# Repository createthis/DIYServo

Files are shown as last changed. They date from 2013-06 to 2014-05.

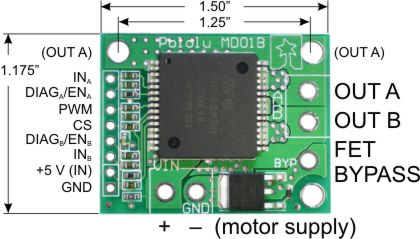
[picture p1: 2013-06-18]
docs/pololu_mdb01_pinout.jpg

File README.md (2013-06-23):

DIYServo
========

http://www.diyservo.com

DIY Servo Project - Create your own servo using any motor of your choosing

This servo uses an Arduino Nano as a controller, and a Pololu MD01B as a motor driver.
The prototype uses a Banebots P60 gearbox (planetary gearing) mated to an RS555 motor. Substitute any 12V motor
of your choosing. For example, a 12V windshield wiper motor (worm gear) would work, or smaller hobby robotics
motors.

Video of latest gear driven MRE in action:
http://youtu.be/2uWNyV8dUlA

Older video of bearing plate mounted MRE in action:
http://youtu.be/V_V_hvIjvC8

Bill of Materials (BOM): https://docs.google.com/spreadsheet/ccc?key=0AlOm0VEWX2qMdGIxMThxUHNPeFVPeEotaU9RSDRENGc&usp=sharing

<br />This work is licensed under a <a rel="license" href="http://creativecommons.org/licenses/by-sa/3.0/">Creative Commons Attribution-ShareAlike 3.0 Unported License</a>.

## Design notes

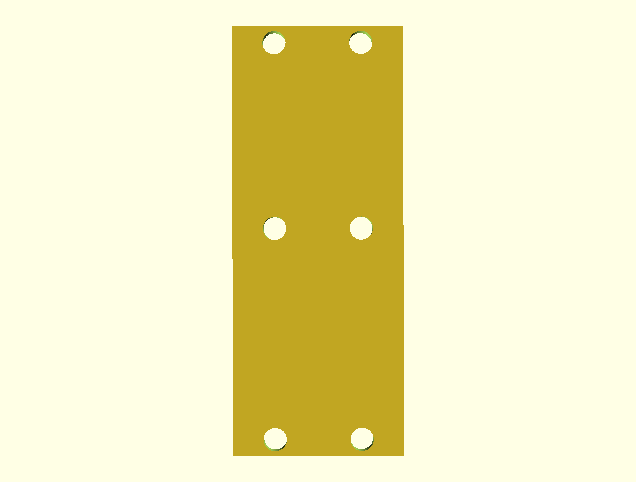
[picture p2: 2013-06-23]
OpenSCAD/motor_plate/motor_plate.png

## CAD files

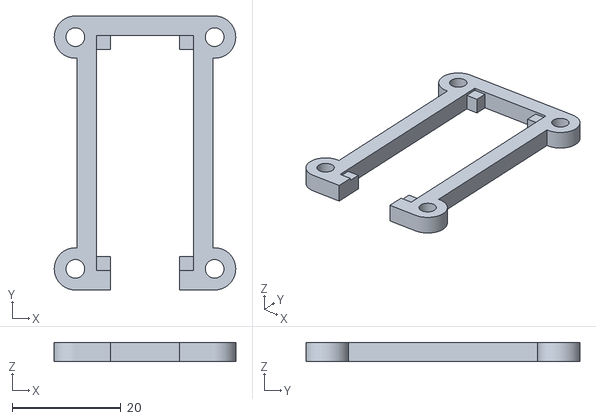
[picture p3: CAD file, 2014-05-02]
OpenSCAD/arduino_nano_enclosure/arduino_nano_enclosure_lid.stl
33.4 x 50.4 x 3.57

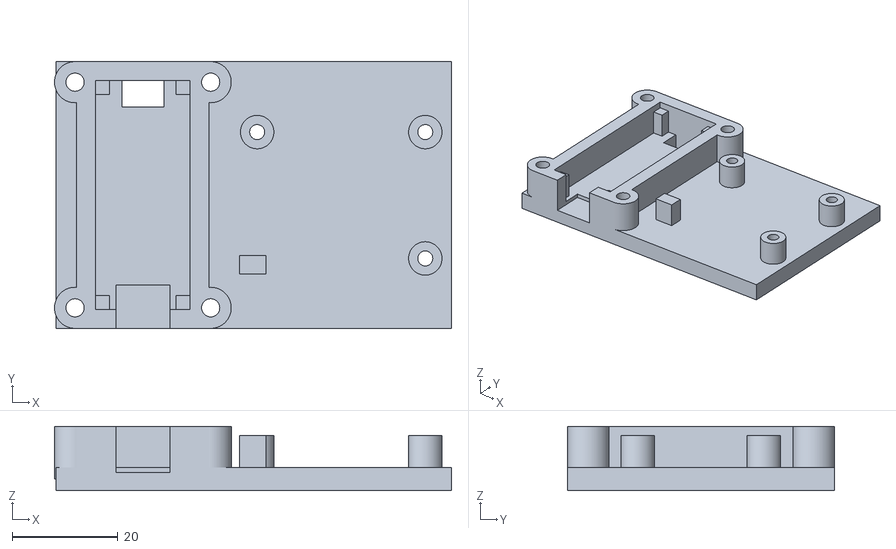
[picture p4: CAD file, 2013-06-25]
OpenSCAD/arduino_nano_pololu_md01b_mounting_plate/arduino_nano_pololu_md01b_mounting_plate_90_center.stl
75.0 x 50.4 x 12.1

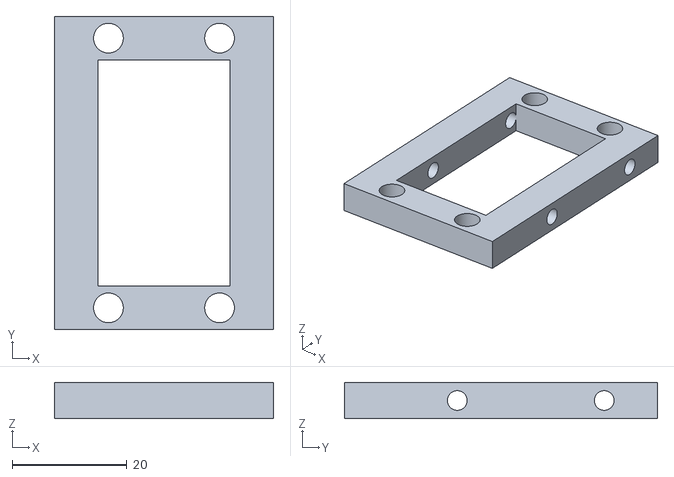
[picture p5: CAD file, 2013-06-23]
OpenSCAD/motor_plate/motor_plate_mounting_bracket.stl
38.2 x 54.6 x 6.29

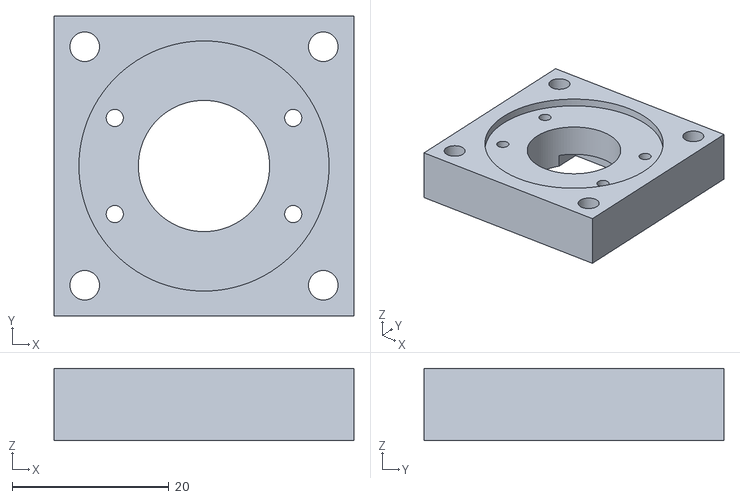
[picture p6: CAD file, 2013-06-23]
OpenSCAD/motor_plate_front/motor_plate_front.stl
38.3 x 38.3 x 9.25

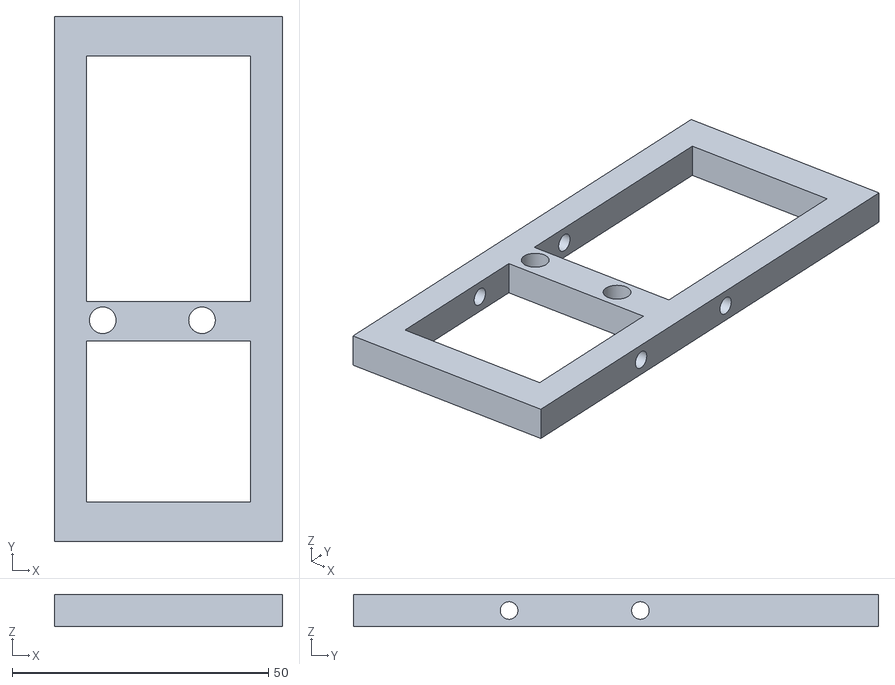
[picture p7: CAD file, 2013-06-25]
OpenSCAD/motor_plate_side/motor_plate_side.stl
44.5 x 102.5 x 6.29

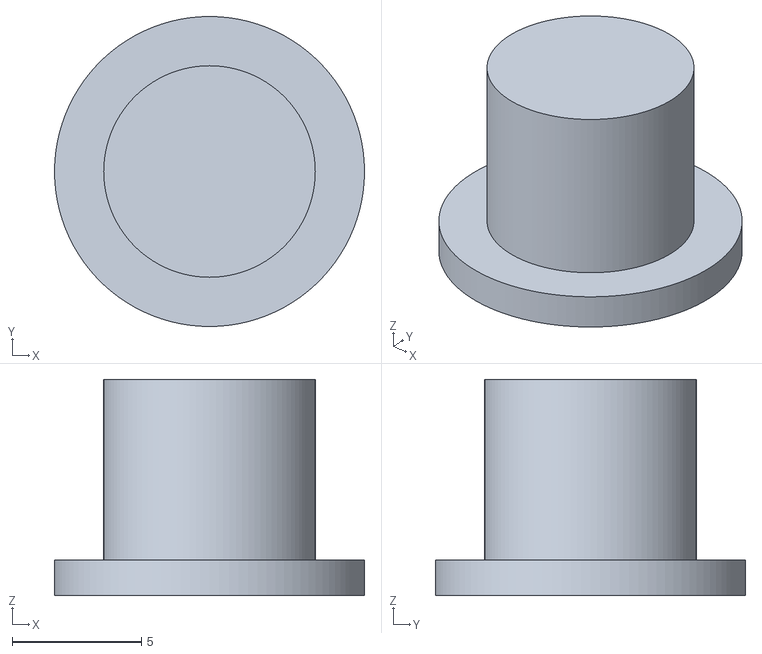
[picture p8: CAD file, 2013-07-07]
OpenSCAD/mre_gear_box/mre_gear_plug.stl
12.0 x 12.0 x 8.38

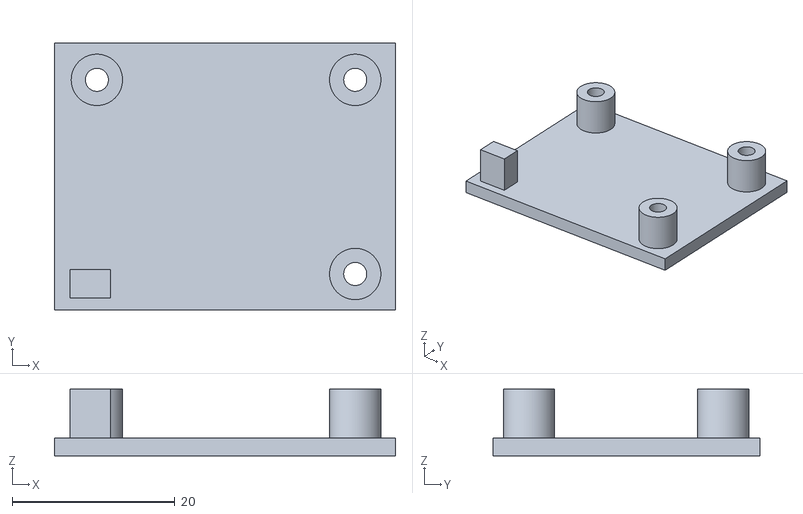
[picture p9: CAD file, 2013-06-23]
OpenSCAD/pololu_md01b_mounting_plate/pololu_md01b_mounting_plate.stl
41.9 x 32.8 x 8.20

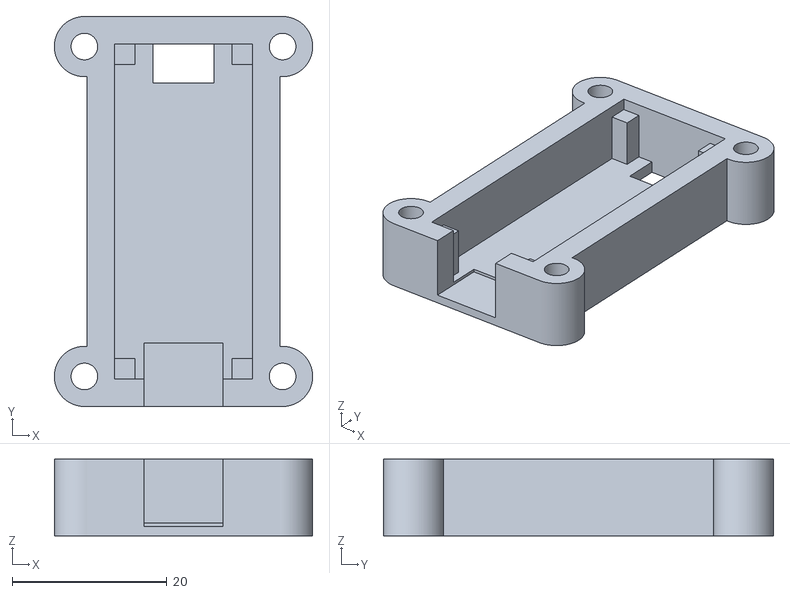
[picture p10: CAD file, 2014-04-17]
OpenSCAD/arduino_nano_enclosure/arduino_nano_enclosure.stl
33.4 x 50.4 x 9.94

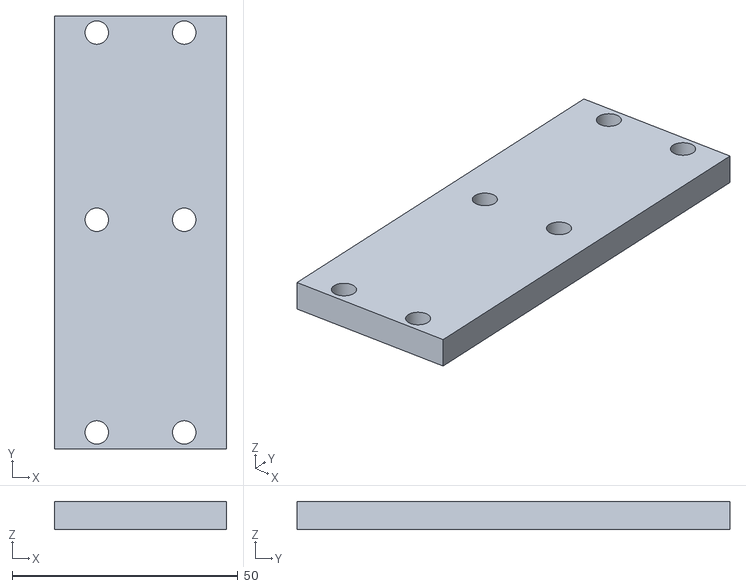
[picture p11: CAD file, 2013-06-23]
OpenSCAD/motor_plate/motor_plate.stl
38.2 x 95.9 x 6.29

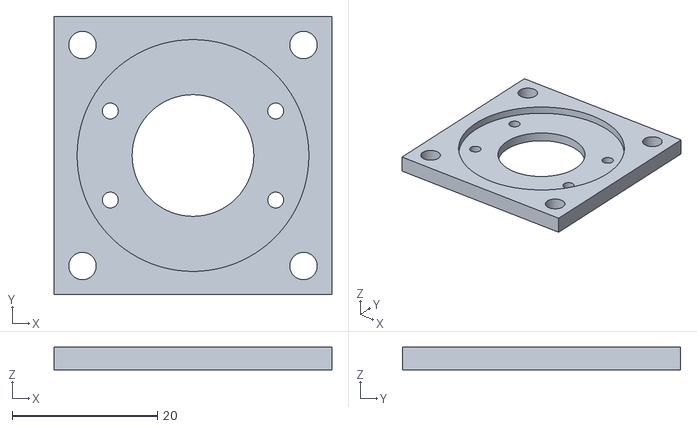
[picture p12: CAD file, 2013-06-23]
OpenSCAD/motor_plate_front/motor_plate_front_bottom.stl
38.3 x 38.3 x 3.12

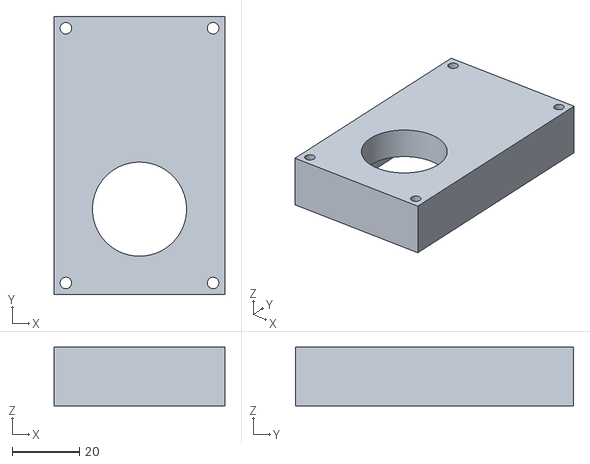
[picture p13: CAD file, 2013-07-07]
OpenSCAD/mre_gear_box/gearbox_cover.stl
50.8 x 82.8 x 17.6

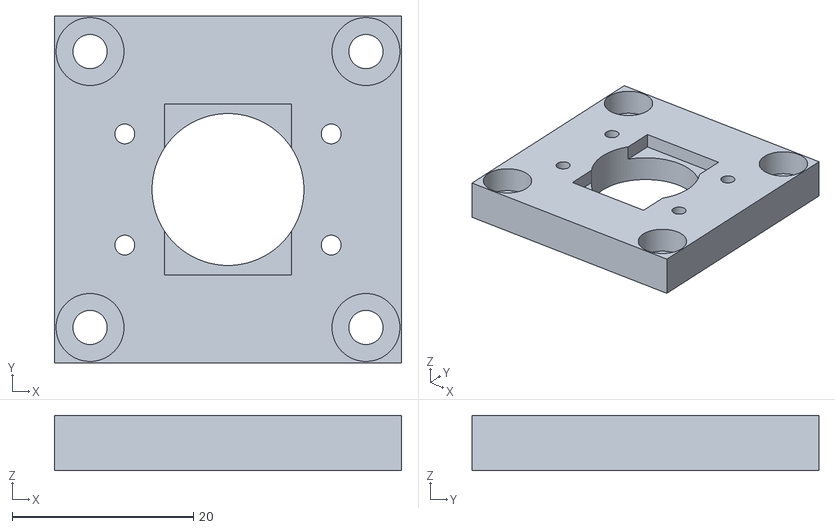
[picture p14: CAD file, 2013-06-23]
OpenSCAD/motor_plate_front/motor_plate_front_top.stl
38.3 x 38.3 x 6.12

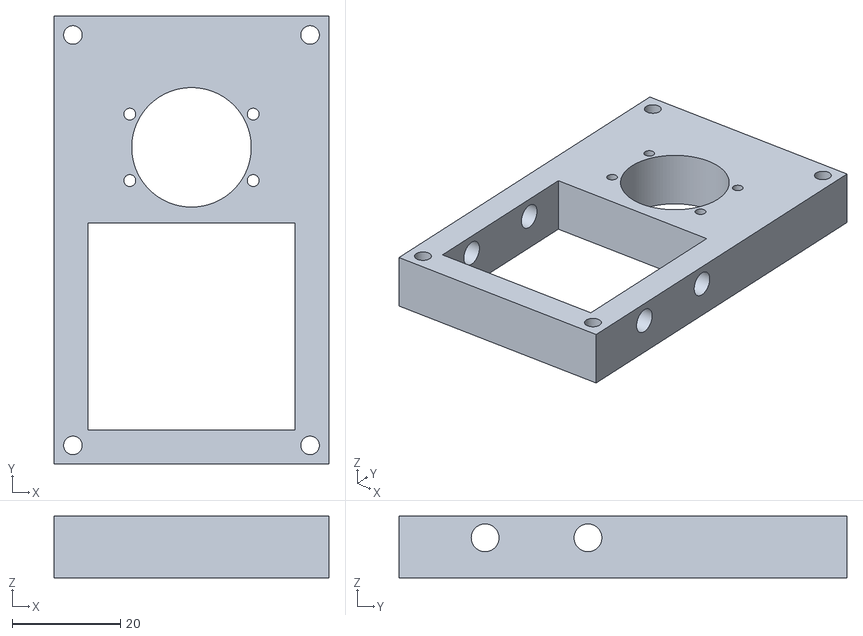
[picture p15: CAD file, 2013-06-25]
OpenSCAD/mre_gear_box/bearing_block.stl
50.8 x 82.8 x 11.4

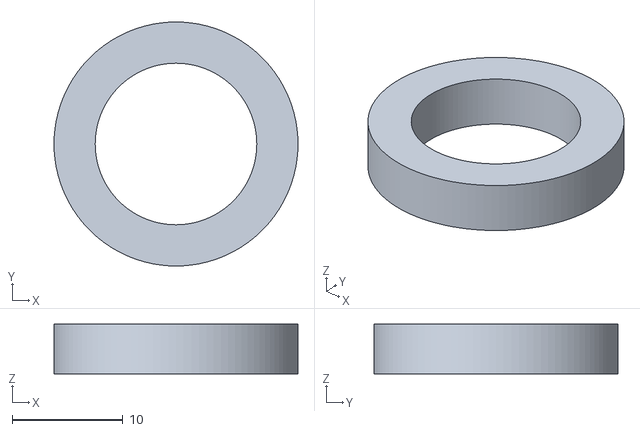
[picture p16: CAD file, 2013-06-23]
OpenSCAD/mre_gear_box/bearing_spacer.stl
22.1 x 22.1 x 4.48

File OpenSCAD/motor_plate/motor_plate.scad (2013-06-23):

/* Copyright 2013 CreateThis.com
 * All Rights Reserved
 */

include <../resolution.scad>
include <motor_plate_dimensions.scad>

// Do It
difference(){
  cube(size = [dimension_width,dimension_length,dimension_thickness], center = true);

  // holes

  // top
  // right
  translate(v = [ dimension_width_center_to_hole_right,dimension_length_middle_to_top_hole_center,0]) {
    cylinder(h = dimension_thickness,r = dimension_hole_radius_scaled,center = true, $fn = resolution);
  }
  // left
  translate(v = [ -dimension_width_center_to_hole_right,dimension_length_middle_to_top_hole_center,0]) {
    cylinder(h = dimension_thickness,r = dimension_hole_radius_scaled,center = true, $fn = resolution);
  }

  // bottom
  // right
  translate(v = [ dimension_width_center_to_hole_right,-dimension_length_middle_to_top_hole_center,0]) {
    cylinder(h = dimension_thickness,r = dimension_hole_radius_scaled,center = true, $fn = resolution);
  }
  // left
  translate(v = [ -dimension_width_center_to_hole_right,-dimension_length_middle_to_top_hole_center,0]) {
    cylinder(h = dimension_thickness,r = dimension_hole_radius_scaled,center = true, $fn = resolution);
  }

  // middle
  // right
  translate(v = [ dimension_width_center_to_hole_right,dimension_length_middle_to_middle_hole_center,0]) {
    cylinder(h = dimension_thickness,r = dimension_hole_radius_scaled,center = true, $fn = resolution);
  }
  // left
  translate(v = [ -dimension_width_center_to_hole_right,dimension_length_middle_to_middle_hole_center,0]) {
    cylinder(h = dimension_thickness,r = dimension_hole_radius_scaled,center = true, $fn = resolution);
  }
}

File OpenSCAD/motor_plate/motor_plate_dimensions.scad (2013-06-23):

/* Copyright 2013 CreateThis.com
 * All Rights Reserved
 */

include <../resolution.scad>

/* Motor plate looks like this:
 *
 * +------+
 * |o    o| top
 * |      |
 * |      |
 * |o    o| middle
 * |      |
 * |      |
 * |      |
 * |o    o| bottom
 * +------+
 */

// Measured Dimensions
dimension_width = 38.18;
dimension_length = 95.94;
dimension_thickness = 6.29;
dimension_hole_diameter = 4.71; // This accepts a #10-32 x 1/2" screw.
dimension_top_to_hole = 1.32;
dimension_side_to_hole = 7.05;
dimension_middle_top_to_hole = 1.42;
dimension_bottom_to_middle_top = 54.57;
dimension_middle_plate_length = 7.58;
dimension_side_screw_hole_diameter = 3.43; // This accepts a #6-32 screw

// Calculated Dimensions Big Plate
dimension_hole_diameter_scaled = dimension_hole_diameter * 1.10; // Add 10% to compensate for printer overflow
dimension_hole_radius = dimension_hole_diameter / 2;
dimension_hole_radius_scaled = dimension_hole_diameter_scaled / 2;
dimension_length_middle_to_top_hole_center = dimension_length / 2 - (dimension_top_to_hole + dimension_hole_radius);
dimension_length_middle_to_middle_hole_center = (dimension_bottom_to_middle_top - dimension_middle_top_to_hole - dimension_hole_radius) - dimension_length / 2;
dimension_width_center_to_hole_right = dimension_width / 2 - dimension_side_to_hole - dimension_hole_radius;

// Calculated Dimensions Gearbox Plate
dimension_gearbox_length = dimension_bottom_to_middle_top;
dimension_gearbox_middle_to_top_hole_center = dimension_gearbox_length / 2 - (dimension_middle_top_to_hole + dimension_hole_radius);
dimension_side_screw_hole_radius = dimension_side_screw_hole_diameter / 2;
dimension_gearbox_through_hole_y = dimension_gearbox_length / 2 - dimension_middle_plate_length - dimension_side_screw_hole_radius;

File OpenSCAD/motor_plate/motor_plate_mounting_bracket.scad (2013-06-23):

/* Copyright 2013 CreateThis.com
 * All Rights Reserved
 */

include <../resolution.scad>
include <motor_plate_dimensions.scad>
use <../arduino_nano_enclosure/arduino_nano_enclosure.scad>

// Do It
difference(){
  cube(size = [dimension_width,dimension_gearbox_length,dimension_thickness], center = true);

  // holes

  // bottom
  // right
  translate(v = [ dimension_width_center_to_hole_right,-dimension_gearbox_middle_to_top_hole_center,0]) {
    cylinder(h = dimension_thickness,r = dimension_hole_radius_scaled,center = true, $fn = resolution);
  }
  // left
  translate(v = [ -dimension_width_center_to_hole_right,-dimension_gearbox_middle_to_top_hole_center,0]) {
    cylinder(h = dimension_thickness,r = dimension_hole_radius_scaled,center = true, $fn = resolution);
  }

  // middle
  // right
  translate(v = [ dimension_width_center_to_hole_right,dimension_gearbox_middle_to_top_hole_center,0]) {
    cylinder(h = dimension_thickness,r = dimension_hole_radius_scaled,center = true, $fn = resolution);
  }
  // left
  translate(v = [ -dimension_width_center_to_hole_right,dimension_gearbox_middle_to_top_hole_center,0]) {
    cylinder(h = dimension_thickness,r = dimension_hole_radius_scaled,center = true, $fn = resolution);
  }

  // side top
  translate(v = [0,dimension_gearbox_through_hole_y,0]) {
    rotate(a=90, v=[0,1,0]) {
      cylinder(h = dimension_width + 0.0001 /* OpenSCAD math bug */,r = dimension_side_screw_hole_radius,center = true, $fn = resolution);
    }
  }

  translate(v = [0,dimension_gearbox_through_hole_y - arduino_nano_enclosure_distance_between_holes_width(),0]) {
    rotate(a=90, v=[0,1,0]) {
      cylinder(h = dimension_width + 0.0001 /* OpenSCAD math bug */,r = dimension_side_screw_hole_radius,center = true, $fn = resolution);
    }
  }

  // Cut hole in middle for faster print times and less waste
  cube(size = [dimension_width - dimension_middle_plate_length * 2,dimension_gearbox_length - dimension_middle_plate_length * 2,dimension_thickness], center = true);
}

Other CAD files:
OpenSCAD/mre_gear_box/bearing_spacer_plate.stl
OpenSCAD/mre_gear_box/mre_gear.stl
OpenSCAD/mre_gear_box/output_shaft_gear.stl
OpenSCAD/motor_plate_front/motor_plate_front.scad
OpenSCAD/arduino_nano_enclosure/arduino_nano_enclosure.scad
OpenSCAD/arduino_nano_enclosure/arduino_nano_enclosure_dimensions.scad
OpenSCAD/arduino_nano_enclosure/arduino_nano_enclosure_lid.scad
OpenSCAD/arduino_nano_pololu_md01b_mounting_plate/arduino_nano_pololu_md01b_mounting_plate_90.scad
OpenSCAD/arduino_nano_pololu_md01b_mounting_plate/arduino_nano_pololu_md01b_mounting_plate_90_center.scad
OpenSCAD/banebots/p60.scad
OpenSCAD/motor_plate_side/motor_plate_side.scad
OpenSCAD/mre_gear_box/bearing_block.scad
OpenSCAD/mre_gear_box/bearing_block_dimensions.scad
OpenSCAD/mre_gear_box/bearing_spacer.scad
OpenSCAD/mre_gear_box/bearing_spacer_plate.scad
OpenSCAD/mre_gear_box/gear_dimensions.scad
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

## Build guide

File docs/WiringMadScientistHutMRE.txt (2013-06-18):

I've gotten an AS5040 10-bit magnetic rotary encoder, and an AS5045 12-bit, working, checking all the non-programmed interfaces. Both can be one-time programmed to output different code schemes, but they're not very useful for what I need so I'm not messing with them.
In both cases I piggybacked the chip/breakout board off an Arduino, using the 3.3v supply. I rather randomly chose to use pins 2, 6, and 7 of the Arduino for the digital input: 6 is a chip select that also signals the start of an interface round, 7 acts as the clock from the Arduino to the chip, and 2 acts as the data transfer from the chip to the Arduino. These are trivially remapped.
The code includes a debug setting that'll print out any faults the AS504x notices, but if you turn off the debug setting you'll just get degrees out. It reads from the chip and transmits to the host computer roughly once a second.

-- John, Mon Dec 13, 2010 11:14 pm
   http://www.madscientisthut.com

More succinctly:
  Arduino Nano - AS5040 Board
           GND - GND
           3v3 - VCC (+3.3v)
             2 - SD Out
             6 - CSEL
             7 - CLK_IN

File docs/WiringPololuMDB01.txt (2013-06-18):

Arduino Nano - Pololu MDB01
          10 - INa
          11 - PWM
          12 - INb
          5V - +5V (IN)
         GND - GND

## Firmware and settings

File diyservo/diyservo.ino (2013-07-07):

/*
   DIY Servo - Arduino driving VNH2SP30 Motor Driver Carrier MD01B

   This work is licensed under the Creative Commons Attribution-ShareAlike 3.0 Unported License. To view a copy of this license, visit http://creativecommons.org/licenses/by-sa/3.0/ or send a letter to Creative Commons, 444 Castro Street, Suite 900, Mountain View, California, 94041, USA.
 */

#include <PololuDriver.h>
#include <PID_v1.h>
#include <PID_AutoTune_v0.h>

#define ENCODER_A_PIN 2
#define ENCODER_B_PIN 3

// PID Variables
double currentPosition = 310;
double distance = 0; // distance in degrees from currentPosition to positionGoal
double distanceGoal = 0; // we always want the motor to be right on the money
double motorSpeed = 0;
double positionGoal = 120;
double kp=0.000001, ki=0, kd=40;
/* kd=0.005 kind of stable */
double upperSpeedLimit = 255;
double lowerSpeedLimit = 33;

// AutoTune Library Variables
double aTuneStep=80, aTuneNoise=1, aTuneStartValue=(upperSpeedLimit - lowerSpeedLimit) / 2 + lowerSpeedLimit;
unsigned int aTuneLookBack=20;
byte ATuneModeRemember=2;

PololuDriver myPololuDriver(11,10,12); // initialize instance of class

const int ledPin = 13; //LED connected to digital pin 13
const int clockPin = 7; //output to clock
const int CSnPin = 6; //output to chip select
const int inputPin = 2; //read AS5040

int debug = 1; //SET THIS TO 0 TO DISABLE PRINTING OF ERROR CODES
boolean tuning = false; // Set this to true to autotune PID values

String currentState = "stop";
String lastState = "stop";
long lastAngle = 0;

//Specify the links and initial tuning parameters
PID myPID(&distance, &motorSpeed, &distanceGoal,kp,ki,kd, DIRECT);
PID_ATune aTune(&currentPosition, &motorSpeed);

// the setup routine runs once when you press reset:
void setup() { 
  Serial.begin(19200);
  Serial.setTimeout(50);
  Serial.println("Started");

  pinMode(ENCODER_A_PIN, INPUT);
  pinMode(ENCODER_B_PIN, INPUT);

  pinMode(ledPin, OUTPUT); // visual signal of I/O to chip
  pinMode(clockPin, OUTPUT); // SCK
  pinMode(CSnPin, OUTPUT); // CSn -- has to toggle high and low to signal chip to start data transfer
  pinMode(inputPin, INPUT); // SDA

  myPololuDriver.Run(POLOLU_STOP);

  currentPosition = read_angle();

  //turn the PID on
  myPID.SetMode(AUTOMATIC);
  myPID.SetOutputLimits(lowerSpeedLimit,upperSpeedLimit);

  if(tuning)
  {
    tuning=false;
    changeAutoTune();
    tuning=true;
    Serial.println("tuning mode");
  }
}

long angle_diff(long angle1, long angle2) {
  return (abs(angle1 + 180 - angle2) % 360 - 180); 
}

boolean should_go_forward(long angle1, long angle2) {
  return ((angle1 - angle2 + 360)%360>180);
}

// the loop routine runs over and over again forever:
void loop() {
  lastState = currentState;

  currentPosition = read_angle();
  distance = abs(angle_diff(currentPosition, positionGoal));

  if(tuning)
  {
    byte val = (aTune.Runtime());
    if (val!=0)
    {
      tuning = false;
    }
    if(!tuning)
    { //we're done, set the tuning parameters
      kp = aTune.GetKp();
      ki = aTune.GetKi();
      kd = aTune.GetKd();
      myPID.SetTunings(kp,ki,kd);
      AutoTuneHelper(false);
      Serial.print("kp: ");Serial.print(myPID.GetKp());Serial.print(" ");
      Serial.print("ki: ");Serial.print(myPID.GetKi());Serial.print(" ");
      Serial.print("kd: ");Serial.print(myPID.GetKd());Serial.println();
    }
  }
  else myPID.Compute();

  myPololuDriver.SetSpeed((byte) motorSpeed);

  // send data only when you receive data:
  if (Serial.available() > 0) {
    myPololuDriver.Run(POLOLU_STOP);
    currentState = "stop";
    lastState = "stop";
    // read the incoming byte:
    positionGoal = (double) Serial.parseInt();

    // say what you got:
    Serial.print("I received: ");
    Serial.println(positionGoal, DEC);
    Serial.print("myangle: ");
    Serial.println(currentPosition, DEC);

    //if((positionGoal==0 && !tuning) || (positionGoal!=0 && tuning))changeAutoTune();
  } else {
    if (abs(angle_diff(lastAngle,currentPosition)) > 1) {
      //Serial.print("angle_diff: ");
      //Serial.println(angle_diff(currentPosition, positionGoal), DEC);
    }

    if(tuning){
      //Serial.println("tuning mode");
    }
  }

  if (abs(angle_diff(currentPosition, positionGoal)) == 0 /* 0 degree hysterisis */) {
    if (lastState != "stop") {
/*
      Serial.println("stop");
      Serial.print("currentPosition: ");
      Serial.println(currentPosition, DEC);
*/
      myPololuDriver.SetSpeed((byte)motorSpeed);
      currentState = "stop";
      myPololuDriver.Run(POLOLU_STOP);
    }
  } else {
    if (!should_go_forward(currentPosition, positionGoal)) {
/*
      Serial.print("should go forward");
      Serial.print(",distance=");
      Serial.print(distance,DEC);
      Serial.print(",motorSpeed=");
      Serial.print(motorSpeed,DEC);
      Serial.print(",currentPosition=");
      Serial.print(currentPosition,DEC);
      Serial.print(",positionGoal=");
      Serial.println(positionGoal,DEC);
*/
      if (lastState != "forward") {
//        Serial.println("forward");
        myPololuDriver.SetSpeed((byte)motorSpeed);
        currentState = "forward";
        myPololuDriver.Run(POLOLU_FORWARD);
      }
    } else {
/*
      Serial.print("should reverse");
      Serial.print(",distance=");
      Serial.print(distance,DEC);
      Serial.print(",motorSpeed=");
      Serial.print(motorSpeed,DEC);
      Serial.print(",currentPosition=");
      Serial.print(currentPosition,DEC);
      Serial.print(",positionGoal=");
      Serial.println(positionGoal,DEC);
*/

      if (lastState != "reverse") {
//        Serial.println("reverse");
        myPololuDriver.SetSpeed((byte)motorSpeed);
        currentState = "reverse";
        myPololuDriver.Run(POLOLU_REVERSE);
      }
    }
  }
  lastAngle = currentPosition;
}

long read_angle()
{
  int inputstream = 0; //one bit read from pin
  long packeddata = 0; //two bytes concatenated from inputstream
  long angle = 0; //holds processed angle value
  long anglemask = 65472; //0x1111111111000000: mask to obtain first 10 digits with position info
  long statusmask = 63; //0x000000000111111; mask to obtain last 6 digits containing status info
  long statusbits; //holds status/error information
  int DECn; //bit holding decreasing magnet field error data
  int INCn; //bit holding increasing magnet field error data
  int OCF; //bit holding startup-valid bit
  int COF; //bit holding cordic DSP processing error data
  int LIN; //bit holding magnet field displacement error data
  int shortdelay = 40; // this is the microseconds of delay in the data clock
  int longdelay = 1; // this is the milliseconds between readings

  // CSn needs to cycle from high to low to initiate transfer. Then clock cycles. As it goes high
  // again, data will appear on sda
  digitalWrite(CSnPin, HIGH); // CSn high
  digitalWrite(clockPin, HIGH); // CLK high
  //delay(longdelay);// time between readings
  delayMicroseconds(shortdelay); // delay for chip initialization
  digitalWrite(ledPin, HIGH); // signal start of transfer with LED
  digitalWrite(CSnPin, LOW); // CSn low: start of transfer
  delayMicroseconds(shortdelay); // delay for chip initialization
  digitalWrite(clockPin, LOW); // CLK goes low: start clocking
  delayMicroseconds(shortdelay); // hold low
  for (int x=0; x <16; x++) // clock signal, 16 transitions, output to clock pin
  {
    digitalWrite(clockPin, HIGH); //clock goes high
    delayMicroseconds(shortdelay); // 
    inputstream =digitalRead(inputPin); // read one bit of data from pin
    //Serial.print(inputstream, DEC);
    packeddata = ((packeddata << 1) + inputstream);// left-shift summing variable, add pin value
    digitalWrite(clockPin, LOW);
    delayMicroseconds(shortdelay); // end of one clock cycle
  }
  // end of entire clock cycle
  //Serial.println(" ");
  digitalWrite(ledPin, LOW); // signal end of transmission
  // lots of diagnostics for verifying bitwise operations
  //Serial.print("packed:");
  //Serial.println(packeddata,DEC);
  //Serial.print("pack bin: ");
  // Serial.println(packeddata,BIN);
  angle = packeddata & anglemask; // mask rightmost 6 digits of packeddata to zero, into angle.
  //Serial.print("mask: ");
  //Serial.println(anglemask, BIN);
  //Serial.print("bin angle:");
  //Serial.println(angle, BIN);
  //Serial.print("angle: ");
  //Serial.println(angle, DEC);
  angle = (angle >> 6); // shift 16-digit angle right 6 digits to form 10-digit value
  //Serial.print("angleshft:");
  //Serial.println(angle, BIN);
  //Serial.print("angledec: ");
  //Serial.println(angle, DEC);
  angle = angle * 0.3515; // angle * (360/1024) == actual degrees
  //Serial.print("angle: "); // and, finally, print it.
  //Serial.println(angle, DEC);
  //Serial.println("--------------------");
  //Serial.print("raw: "); // this was the prefix for the bit-by-bit diag output inside the loop.
  if (debug)
  {
    statusbits = packeddata & statusmask;
    DECn = statusbits & 2; // goes high if magnet moved away from IC
    INCn = statusbits & 4; // goes high if magnet moved towards IC
    LIN = statusbits & 8; // goes high for linearity alarm
    COF = statusbits & 16; // goes high for cordic overflow: data invalid
    OCF = statusbits & 32; // this is 1 when the chip startup is finished.
    if (DECn && INCn) { Serial.println("magnet moved out of range"); }
    else
    {
      if (DECn) { Serial.println("magnet moved away from chip"); }
      if (INCn) { Serial.println("magnet moved towards chip"); }
    }
    if (LIN) { Serial.println("linearity alarm: magnet misaligned? Data questionable."); }
    if (COF) { Serial.println("cordic overflow: magnet misaligned? Data invalid."); }
  }

  return (double) angle;

  packeddata = 0; // reset both variables to zero so they don't just accumulate
  angle = 0;
}

void changeAutoTune()
{
  if(!tuning)
  {
    //Set the output to the desired starting frequency.
    motorSpeed=aTuneStartValue;
    aTune.SetNoiseBand(aTuneNoise);
    aTune.SetOutputStep(aTuneStep);
    aTune.SetLookbackSec((int)aTuneLookBack);
    AutoTuneHelper(true);
    tuning = true;
  }
  else
  { //cancel autotune
    aTune.Cancel();
    tuning = false;
    AutoTuneHelper(false);
  }
}

void AutoTuneHelper(boolean start)
{
  if(start)
    ATuneModeRemember = myPID.GetMode();
  else
    myPID.SetMode(ATuneModeRemember);
}

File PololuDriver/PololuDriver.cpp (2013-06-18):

#include "PololuDriver.h"

PololuDriver::PololuDriver(byte pwmPin, byte inA, byte inB)
{
	m_pwm = pwmPin;
	m_inA = inA;
	m_inB = inB;
	
	pinMode(inA, OUTPUT); //can send +/0 voltage 3.3v/0
	pinMode(inB, OUTPUT);
	analogWrite(m_pwm, 0);
}

void PololuDriver::SetSpeed(byte speed)
{	
	analogWrite(m_pwm, speed);
}

void PololuDriver::Run(byte direction)
{	
	switch (direction)
	{
		case POLOLU_STOP:
			digitalWrite(m_inA, LOW);
			digitalWrite(m_inB, LOW);
			break;
		case POLOLU_FORWARD:
			digitalWrite(m_inA, HIGH);
			digitalWrite(m_inB, LOW);
			break;
		case POLOLU_REVERSE	:
			digitalWrite(m_inA, LOW);
			digitalWrite(m_inB, HIGH);
			break;
	}
}

void PololuDriver::Run(byte direction, byte speed)
{
	SetSpeed(speed);
	Run(direction);
}

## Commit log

2013-06-18 add BOM
2013-06-23 Arduino is quirky and requires sketches to be in a directory of the same name. Go figure.
2013-06-23 Add OpenSCAD source code. This is the code necessary to 3d print all of the plastics for the project.
    [arduino_nano_enclosure.scad, arduino_nano_enclosure.stl, arduino_nano_enclosure_dimensions.scad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]
2013-06-24 Add side motor plate
    [bearing_block.scad, motor_plate_side.scad, motor_plate_side.stl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]
2013-06-25 Add a basic modeling of the p60 gearbox. This should help people visualize the dimensions coming from the p60 module.
    [p60.scad]
2013-06-25 tweak the scale factor to compensate for my inaccurate hobby printer
    [motor_plate_side.scad, p60.scad]
2013-06-25 update stl for hobby printer scale factor.
    [motor_plate_side.stl]
2013-06-25 move the md01b to the center of the board so we can add a case later.
    [arduino_nano_enclosure.scad, arduino_nano_pololu_md01b_mounting_plate.scad, arduino_nano_pololu_md01b_mounting_plate.stl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]
2013-06-25 Add bottom and lid mounting holes to bearing plate.
    [bearing_block.scad, bearing_block.stl, bearing_block_dimensions.scad]
2013-06-25 Speed up serial input: http://forum.arduino.cc/index.php?topic=99336.0
2013-07-04 Commit my work in progress attempt at a PID controller.
2013-07-04 Add PID based servo control. It needs some tuning work as it's overshooting a lot and bouncing, but I think that may be resolved with the intelligent use of motor braking. Need to think about how to 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
    [diyservo.ino]
2013-07-07 Feature #1047 - Make 3d printed nylon gears and gearbox to drive MRE
    [gearbox_cover.scad, gearbox_cover.stl, gearbox_cover_dimensions.scad]
2013-07-07 Add a 2mm airspace between the cover and the gear. This will be filled by the bearing plug.
    [gearbox_cover.stl, gearbox_cover_dimensions.scad]
2013-07-07 Add a recess in the bearing cover so the bearing rotates freely.
    [gearbox_cover.scad, gearbox_cover.stl, gearbox_cover_dimensions.scad]
2013-07-07 Add mre gearbox plug. This is the part that secures the mre gear from the mre gearbox cover side and keeps it from wiggling out of it's slot.
    [gearbox_cover_dimensions.scad, mre_gear_plug.scad, mre_gear_plug.stl]
2013-07-07 This commit brings the performance of the servo up quite a bit. It still bounces, but I've increased the sample rate of the PID algorithm and it's performing better now. The oscillations are much sma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
    I'm seeing now why people say USB isn't a good control mechanism for a
    servo. Every time I send a message via USB it eats a ton of clock
    cycles. I think implementing a standard hobby RC servo protocol and/or
    an I2C interface would be a good idea.
    [diyservo.ino]
2014-04-17 Update stls rendered from latest OpenSCAD and code.
    [arduino_nano_enclosure.stl, arduino_nano_enclosure_lid.stl]
2014-05-02 Lid wasn't fitting. I must have made a typo when copying this over from the original project.
    [arduino_nano_enclosure_dimensions.scad, arduino_nano_enclosure_lid.stl]
